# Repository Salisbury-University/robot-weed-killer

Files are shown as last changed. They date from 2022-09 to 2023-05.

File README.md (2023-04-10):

# Roundup: Robot Control App

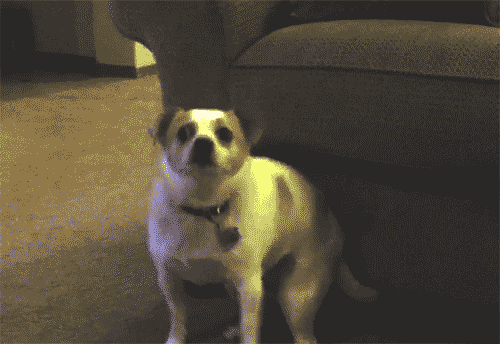
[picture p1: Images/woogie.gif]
Bouncy Dog

Dancing Dog

https://user-images.githubusercontent.com/95944392/224509408-8cf81484-2df1-4522-b72b-3398e59669f4.mp4

https://user-images.githubusercontent.com/95944392/230803867-7e4617c9-662d-4df7-9e29-15715888454c.mp4

---

## Course: COSC 426
## Client: Dr. Giulia Franchi

## Team: Kids Against Weed

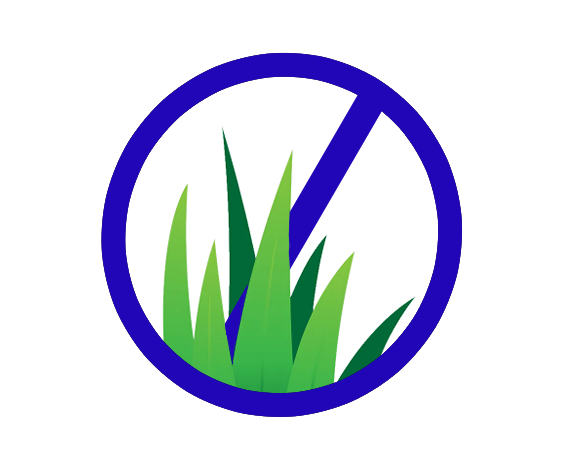
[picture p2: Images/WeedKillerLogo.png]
My Image


---
### Teammates:
* Zach Moore
* Emily Hitchcock
* Garrett Jolly
* Nick Krisulevicz
* Dane Akers
---
## Installation Instructions

```
Currently installed by running command in Flutter: will be updated with final release of product
```
---
## Contents of Repository

### Control

```
Contains Arduino code to control the robot, which includes: Laser Activation/Deactivation, and navigation
control. Both manual control and autonomous control source code resides within this directory
```

### Camera

```
Contains Arduino source code for the ESP32 camera. The ESP32 can broadcast an IP address that can be accessed
remotely from a web browser, i.e: Google Chrome, Firefox, etc. The broadcast streams video with
adjustable resolution and filters.
```

### Images

```
Contains various assets used during development of the app. App logos, splashscreens, and possibly other assets for 
styling are included.
```

### Bluetooth Controller

```
Contains the flutter app created for the project. 
```

### Object Recognition

```
Contains a python script which uses OpenCV and Numpy to detect colors. OpenCV allows for use of a filter that only 
displays certain color hues.
```
---
## Client Updates

```
Meeting 1:
-Team was instructed to finish robot design using existing hardware.
  -Suggested chassis redesign was tabled for later focus by client
  -The team is to continue with acrylic robot chassis currently in use
-Team was given the milestone of having functional autonomous program before 03/17/2023
  -The milestone requirements are as follows:
    -Have a basic autonomous driving algorithm in place
    -Have object recognition algorithm in place
    -

Meeting 2:
-Team demonstrated object recognition to client
-Team demonstrated currently functioning app to the client
-Client laid out expectations between then and the end of the first milestone. 

Meeting 3:
-Details to follow - meeting scheduled for 03/14/2023
```

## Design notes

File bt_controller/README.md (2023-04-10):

# bt_controller

Flutter project that contains the main components of the mobile application. These components are: Menu, Manual Control Screen, and Automated Screen.

## Components

### Menu

* The landing page of the applicationp; this is the first page that shows up when the app is loaded on a mobile phone.
* Allows user to select from manual control of the robot, and automated pathing
* Bluetooth menu button expands popup to select any available devices to pair
* Preferred screen orientation is portrait mode

### Manual Control

* Uses the bluetooth connection data from the menu screen to enable manual control of the robot
* Comprised of a virtual joystick and fire button, layered on top of a webview widget
* Webview used to view camera perspective when controlling the robot.

### Automated View

* Contains a map widget that is currently in a picture-in-a-picture (ideally will expand upon gesture detected and replace camera view)
* No control buttons, will only handle any issues on disconnect
* Back button to return to the menu screen -> currently testing solutions to stop the robot if the user leaves either control page

## Getting Started

If this project is inherited by another Software Engineering Group, visit the docs below to learn how to write a first Flutter app and their "cookbook" for useful samples.

A few resources to get you started if this is your first Flutter project:

- [Lab: Write your first Flutter app](https://docs.flutter.dev/get-started/codelab)
- [Cookbook: Useful Flutter samples](https://docs.flutter.dev/cookbook)
- [Navigator Class: Used to retain data across screens](https://api.flutter.dev/flutter/widgets/Navigator-class.html)

For help getting started with Flutter development, view the
[online documentation](https://docs.flutter.dev/), which offers tutorials,
samples, guidance on mobile development, and a full API reference.

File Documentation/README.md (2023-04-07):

# Roundup App Documentation
---

## Contents

* Wiring Pinouts
* Chassis Weight Distribution
* Installation Instructions

---
This folder will contain all relevant documentation of this project that is not included in the Github Wiki.

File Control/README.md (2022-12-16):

## Car Control

```
* Each folder contains the arduino code required for the vehicle to drive under the control of bluetooth or wired serial 
   connection respectively.

* The serial folder contains the Arduino code for the device to read serial input for driving and laser firing, along 
   with the Python code to drive the car through a command prompt.

    * The Python control functions are deprecated in the sense of they are not tied to the Flutter app build of the 
       project.

* The bluetooth folder contains the Arduino code for the device to read serial input over bluetooth to drive and fire 
   the laser, along with the Python code to initiate a bluetooth connection and send commands to the car. Connection to 
   the bluetooth module is needed to be initiated from device settings beforehand, or Python cannot esablish the 
   conneciton. The com port may need to be adjusted as nessecary.
```

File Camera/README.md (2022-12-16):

## ESP32 Camera

Directory contains the code to run the ESP32 camera.
```
* The camera has a web connection to stream the video to. 
* The video is accessed with the IP address. 
    * Current IP address is ##192.168.4.1
    * The app will connect to the IP address
```

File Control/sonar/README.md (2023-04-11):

#Autonomous control exists in this directory
#The current iteration of autonomous code is in (insert filename.ino here)

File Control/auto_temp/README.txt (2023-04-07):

#This directory does not hold the working autonomous files
#Find the working file in /Control/sonar

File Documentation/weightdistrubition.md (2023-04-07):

# Weight Distribution in New Chassis

## FRONT END:

```Weight of laser: 13.1 oz```

## REAR END:

* Weight of lead cylinder, 3cm diameter, 1cm height: 2.8 oz
* 2x lead cylinder = 4.7 oz
* Arduino mega weight: 1.2 oz
* Power cell weight: 10.4 oz

#### Weight distribution: 13.1 vs 10.4 = 24% more weight on rear end
#### Weight distribution is calculated based on equipment, not weight of chassis or motors & wheels

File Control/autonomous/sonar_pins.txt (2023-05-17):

1st sonar sensor: LEFT FRONT, DIGITAL, echo = 50, trigger = 52, (Original lone sensor)
Left sensor: VCC = Red wire, GND = Green wire

2nd sonar sensor: RIGHT FRONT, DIGITAL, echo = 40, trigger = 42
Right sensor: VCC = Grey wire, GND = Green wire

3rd sonar sensor: REAR, DIGITAL, trigger = 10, echo = 9
Rear sensor: VCC = White wire, GND = Grey wire

WIRING (IN ORDER OF LEFT TO RIGHT)

Left sensor: green, yellow, orange, red

Right sensor: green, blue, purple, grey

Rear sensor: grey, green, purple, white

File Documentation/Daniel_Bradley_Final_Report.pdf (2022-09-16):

SALISBURY UNIVERSITY

# Weed Removal through Laser Technology and Robotic Automation Report

Daniel Bradley
May 20, 2022

### 1. PROJECT GOALS

The primary goal of this research project is to explore an alternative method of weed control via a laser mounted robot which can target and destroy weeds through automation. During the semester I investigated how robotics, automation, and laser technology can be used as a possible method of weed control. While this is not an original idea, the use of robotics in combination with lasers as weed control is very recent. With currenting testing and studies, I believe that the combination of the three fields can be a potent form of disposing weeds, compared to herbicides.

### 2. INTRODUCTION

To control the growth and spread of weeds, accurate targeting of weeds is required. Primary methods of weed control are with herbicides and manual labor. Herbicides being the most convenient option comes at the price of having a negative impact on the surrounding environment. A study by Karl V. Miller shows that the adaptivity of weeds proves to be detrimental to the effectiveness of herbicides when it comes to repeated treatment (Miller 2004). Manual labor requires a heavy investment of time compared to herbicide yet does not harm the environment.

While less common methods are being researched, such as uprooting, an alternative to these methods is laser technology in combination with automation (Kurstjens 2001). The laser will be able precisely target weeds and disrupt their growth. A robot can transport a laser while being piloted through artificial intelligence. According to a study by C.Wöltjen,
damage to the meristem of a weed via diode laser (Figure 1) has shown to inhibit growth.(Wöltjen 2008). If a laser can be efficiently transported and navigated to a weed and fired at the meristem, then it would prove to be an effective way to counter weed growth.

## 3. Design

To achieve automation, the robot had to be able distribute its power supply to an Arduino and control multiple different components to assist in movement and guidance. To be able to move from point a to point b, four TT motors with wheels were required for movement. Two motor controllers were used (one for two motors each) so the Arduino could control the direction in which the motors would spin. The last step of automation was the ability to control the power of the laser independently. This was done by connecting a relay in between the 18650-battery pack and the AC adapter for the laser pointer. With this installed, the Arduino will have control on whether the laser will be on or not.

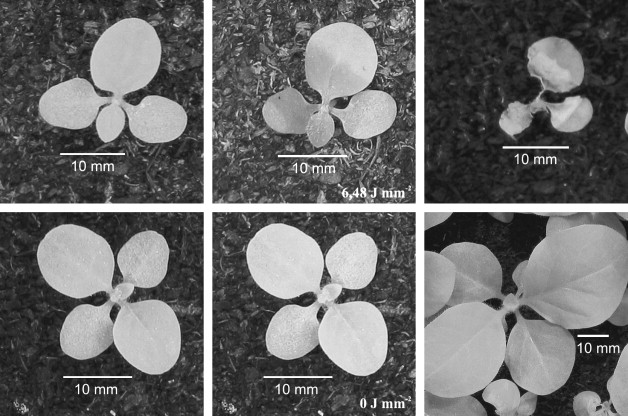
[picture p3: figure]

Figure 1. Top 3 pictures from left to right (untreated, immediately after laser treatment, week after laser treatment). Bottom 3 pictures from left to right( untreated,untreated, a week after).( Mathiassen et al., 2006)

To achieve automation, the robot had to be able distribute its power supply to an Arduino and control multiple different components to assist in movement and guidance. To be able to move from point a to point b, four TT motors with wheels were required for movement. Two motor controllers were used (one for two motors each) so the Arduino could control the direction in which the motors would spin. The last step of automation was the ability to control the power of the laser independently. This was done by connecting a relay in between the 18650-battery pack and the AC adapter for the laser pointer. With this installed, the Arduino will have control on whether the laser will be on or not.

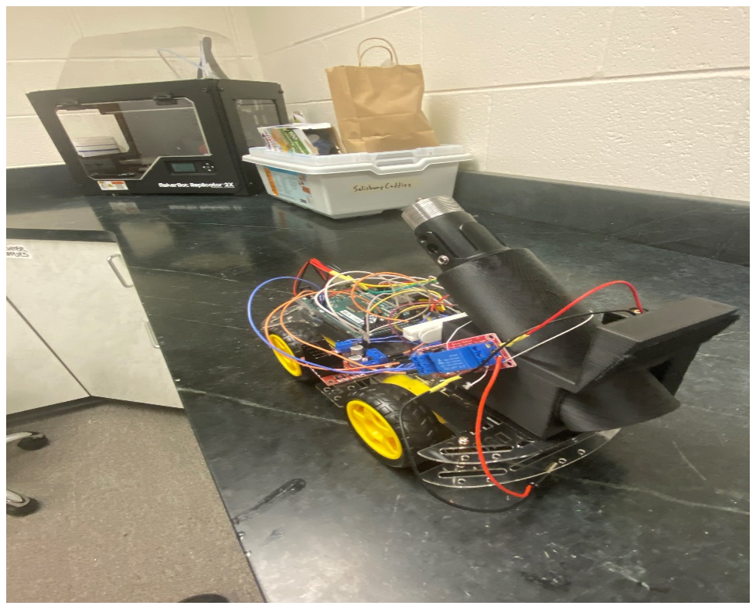
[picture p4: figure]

Figure 2:Laser – Mounted Robot

However, none of this would work without sufficient power supply. Powering the Arduino, two motor controllers, four TT motors, and the relay is done by four 9v batteries taped together in a harness. To power everything together, a breadboard was placed in the center of the robot. Here, all the positive and ground wires of the components and batteries would come together.

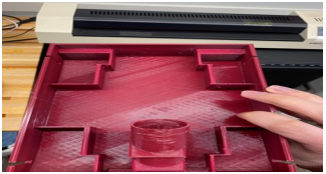
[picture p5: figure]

Figure 3:3D Printed Robot Frame

Initially the design of the robot was going to consist of a 3D printed frame designed in CAD to hold all the components of the robot. These components consist of an Arduino, 4 TT motors with wheels, 2 motor controllers, 4 9V batteries, a protoboard, and a holster to hold the laser. The prints however were not sufficient to hold the laser and other components. This was caused by either misprints by the 3D printer or inaccurate measurements in CAD. Instead, a robot frame was purchased, and a laser holster designed from CAD was 3D printed to be velcroed to the frame.

The plastic frame provided much more space than any of the previous CAD designs. The plastic frame was longer and wider than that the 3D printer workspace could provide, as well as the platform having two layers. The first layer of the plastic frame holds four 9v batteries and four TT motors. The second layer holds the laser holster, the laser, the Arduino, two motor controllers, the breadboard, and the relay. With this set up, I effectively had double the space since some components were in between to two plastic frames.

Starting from the front of the Robot, the laser holster in the centerpiece. The camera, battery pack, relay, breadboard, and laser are all in contact with the holster. While the holster is Velcroed on the frame of the robot, The camera, battery pack, and breadboard are velcroed to the holster itself. For the camera, thin strips of Velcro were attached to the frame of the camera to protect the screen and placed onto the laser holster. Since the wire connecting the battery pack and the relay is lengthy, the battery pack is velcroed to the left side of the holster while the relay is tied to the right side. The Arduino is in a plastic Arduino frame, which is velcroed to the robot frame.

A special note referring to the Velcro of the breadboard, in order to remove the Velcro the tabs on the right hand side of the white Velcro must be pulled to loosen it.

## 4. Components

Laser: A 5W 445 nm diode laser (PL-E Pro series) will be used throughout the project. The idea was that a laser that was strong enough to burn materials such as plants was required. In addition, the laser must have the ability to be controlled through a relay by an Arduino. In my research I found the laser pointer was strong enough to burn basic and organic materials as well as become automated by the Arduino.

3D Printed Laser Holster: Since both the laser and the camera must be in front of the robot, I decided that a holster that could hold both would be beneficial. The holster has a diagonal tube where the laser is placed. The diagonal angle lets the laser shoot in front of the robot and can be aimed into corners where the robot could not physically go. Facing the front of the holster is a platform where the camera is placed. The platform is angled slightly down so that the camera can see the ground in front of the robot where weeds would appear.

Husky Lens Camera: The Husky Camera has two buttons on the top side of the camera, with the screen pointing towards the user. The left side is for selecting different algorithms such as face identification, object identification, object tracking, and color identification. The right button is used to make the camera “learn” whatever is in the highlighted square on the screen. Once is recognizes an object, it will highlight the object on the screen and output information of its position on the XY axis and its size on the screen.

Laser Wiring/Power Procedure: Proper power procedure starts with making sure the cap is not on the laser, this must be twisted off for the laser to work properly. There are two ways to power the laser pointer. The first way is to insert two 18650 batteries into the battery tube and then the tube is twisted onto the laser. Then press the button on the end to the battery tube to power the laser.

The second way to power the laser pointer is through the relay. The AC adapter connected between the relay and the battery pack is inserted into the AC adapter. Insert the two 18650 batteries into the battery pack, then place the AC adapter that connects to the battery back and the laser into the AC port of the laser pointer.

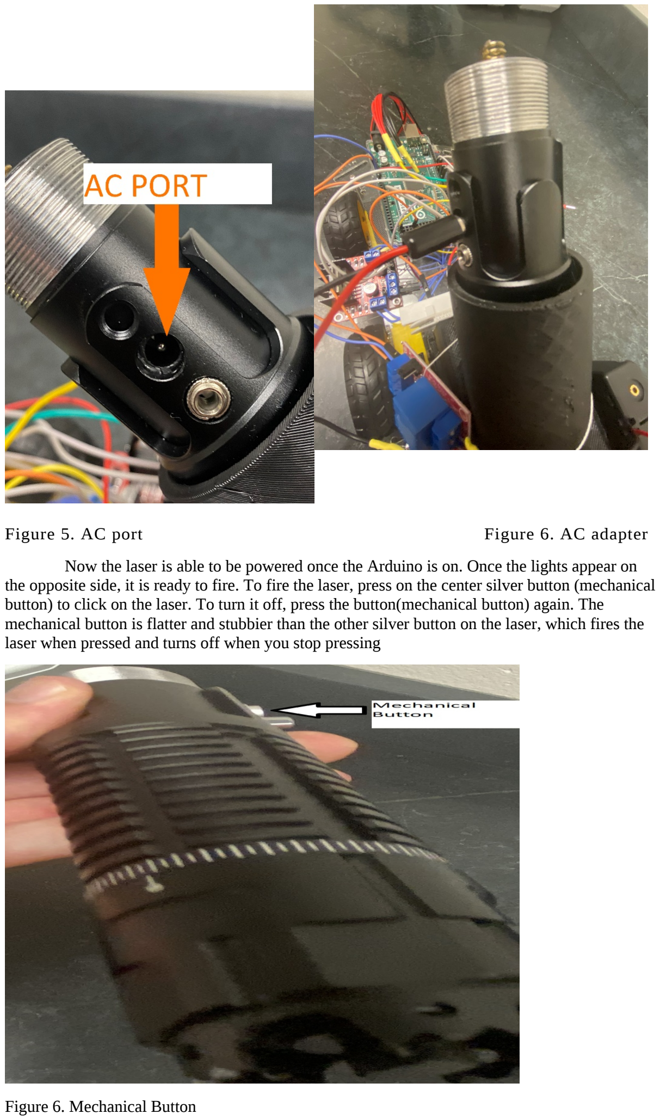
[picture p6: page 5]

Figure 5. AC port | Figure 6. AC adapter

Now the laser is able to be powered once the Arduino is on. Once the lights appear on the opposite side, it is ready to fire. To fire the laser, press on the center silver button (mechanical button) to click on the laser. To turn it off, press the button(mechanical button) again. The mechanical button is flatter and stubbier than the other silver button on the laser, which fires the laser when pressed and turns off when you stop pressing

Figure 6. Mechanical Button

Wiring the Components

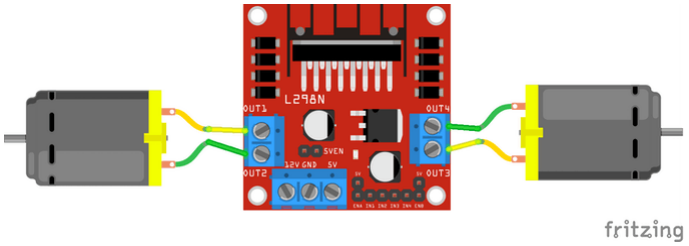
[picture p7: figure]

Figure 7. Wiring from motor controller to motors

## 4. Testing

The first test was the movement of the robot with the laser in the holster. There was initial concern that the laser would be too heavy to transport. However, testing the robot’s movement showed that there was no such issue. At times the wheels would rub against the plastic frame causing stuttering. This was fixed by adjusting the wheel in the motor axis as well as filing down the point of contact between the wheel and the platform.

Once movement was squared away, I connected the Husky Lens camera and had it identify any object that was light green. With the code I used, the robot would rotate left and right if the object was pulled to either side of the screen. Testing on making the robot go forward and backwards based on the distance of the object did not work. More testing is required to see why the robot did not act accordingly.

T h e b r e a d b o a r d i s t h e p r i m a r y s o u r c e o f p o w e r , i t p o w e r s t h e A r d u i n o M e g a , t w o m o t o r
c o n t r o l l e r s , a n d f o u r m o t o r s . A l l t h e p o s i t i v e a n d g r o u n d p o r t s o f t h e s e c o m p o n e n t s w i l l
l i k e l y b e c o n n e c t e d t o t h e b r e a d b o a r d . A s o f n o w t h e r e i s o n l y t h e g r o u n d w i r e f r o m t h e 9 v b a t t e r i e s i n t h e b r e a d b o a r d , o n c e t h e p o s i t i v e w i r e f r o m t h e 9 v b a t t e r i e s i s i n s e r t e d i n t o t h e b r e a d b o a r d t h e r o b o t w i l l b e p o w e r e d . W h i c h i s w h y t h e b e s t p r a c t i c e i s t o h a v e e i t h e r t h e r o b o t p r o p p e d o f f t h e g r o u n d w h e r e t h e w h e e l s h a n g f r e e l y , o r m a k e s u r e t h e c o d e w i l l n o t h a v e t h e r o b o t p e r f o r m a n y u n e x p e c t e d a c t i o n s . T o w i r e t h e m o t o r s t o t h e m o t o r c o n t r o l l e r s , O U T 1 ( o u t p u t 1 ) a n d O U T 2 ( o u t p u t 2 ) m u s t b e

w i r e d t o t h e i n p u t s o f t h e s a m e m o t o r . I n t h e c u r r e n t s t a t e o f t h e r o b o t , t h e o u t p u t s a r e
w i r e d t o t h e p r o p e r m o t o r i n p u t s t o a v o i d c o n f u s i o n i n t h e c o d e . O n c e t w o m o t o r s a r e
w i r e d t o t h e m o t o r c o n t r o l l e r s , t h e g r o u n d a n d t h e 1 2 v p o r t w i l l b e c o n n e c t e d t o t h e
b r e a d b o a r d . T o h a v e t h e A r d u i n o c o n t r o l t h e m o v e m e n t s o f t h e m o t o r s , c o n n e c t
I N 1 , I N 2 , I N 3 , I N 4 ( t h e i n p u t s ) i n t o f o u r s e p a r a t e d i g i t a l p o r t s o n t h e A r d u i n o M e g a . ( T i p : s e t t h e d i g i t a l n u m b e r p o r t a s a v a l u e f o r t h e d e f i n e v a r i a b l e i n c o d e ) .

As mentioned before, the motors require a HIGH,LOW output to go forward. Here in the forward function I set each motors 1,2,3,and 4 to forward. To go backwards I call the Backward function, which sets all to LOW,HIGH. This results in the robot moving backwards.

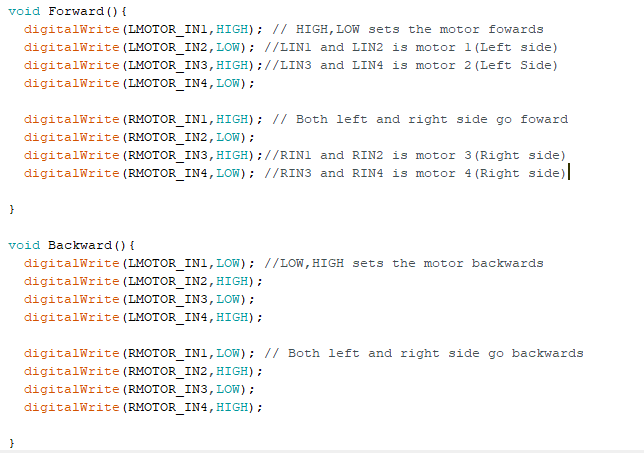
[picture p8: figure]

Figure 8. Forward() and Backward() function

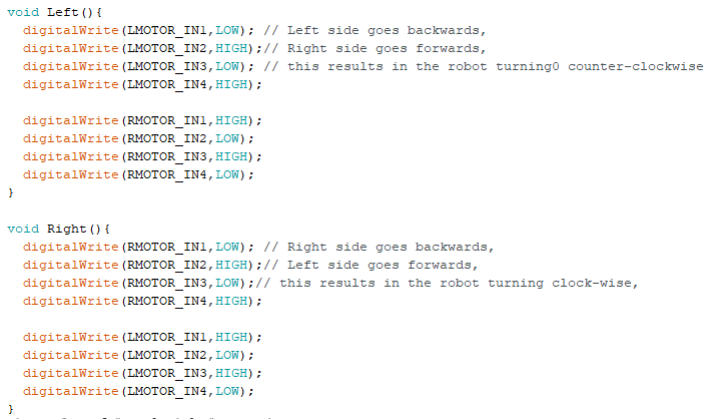
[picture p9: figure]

Figure 9. Left() and Right() Functions

To have the robot rotate, one side must spin in the opposite direction of the other side. To move left(counter -clockwise) the right motors are set to HIGH,LOW to move forward, while the left motors are set to LOW,HIGH to move backwards. The outcome is the robot will begin turning left when the Left() function is called. To have the robot rotate to the right, the motors will have the opposite directions compared to the left turn function. For turning right(clockwise), the right motors will be set to LOW,HIGH to move backwards, while the left motors will be set to HIGH,LOW to move forward. When the Right() function is called the robot will begin to spin right.

The other test had to do with the powering of the laser. Once the laser was connected to the relay. I programmed code to turn the laser on and off in 3 second intervals.

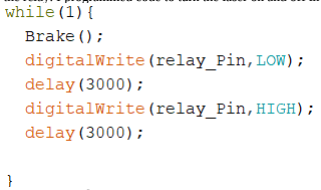
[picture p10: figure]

Figure 10. Relay Loop

In the code above, I have a while loop that last forever. In the while loop I have the Brake function called to cease movement from the robot. Afterwards, I set the relay pin to LOW with digital write then it sleeps for three seconds. The laser remains off for 3 seconds until the next digit write is called. Then the relay pin is set to HIGH and the laser is powered on for three seconds. This will repeat forever until the robot is unplugged. With the digital write function, I can set any conditional to set the relay pin to HIGH. If said condition is not meet, then the relay pin is set to LOW.

## 5. PROGRESS AND RESULTS

As of May 19
th

, the robot is able to move forwards, backwards ,turn right, turn left, and brake while carrying the laser. The robot is also capable of controlling the power to the laser. Also, components are attached to the robot to prevent any damage to the robot. Unfortunately, the Husky Lens camera module had a hardware failure during testing, so testing object tracking and laser activation through color recognition could not be done.

## 6. FUTURE WORKS

For the future, the hardware failure of the Husky Lens should be investigated. During testing of the Husky Camera module the metal components would become very hot, which I believe was the symptom of the problem. Once the camera is powered safely and efficiently, then testing of object tracking and color identification should be a priority.
When object tracking and color identification can be achieved consistently to target weeds, then testing the robot ability to follow along the sidewalk and target weeds should be done. Using the controls of the Husky Camera, the camera can learn the color of weeds using the color identification algorithm. The use of object identification on weeds can also be explored. The goal being able to accurately target weeds, minimize any misfires or overshooting, and minimize deviation from the sidewalk.
Once it can accurately target weeds, the next goal would be to explore a way to avoid obstacles. Since the Husky camera will be used to target weeds, an additional camera would have to be dedicated to obstacle avoidance. An ultrasonic senor would be able the measure the space between the robot and the ground. If an obstacle were in the way, the sensor would detect a difference distance from the distance to the ground. Then the robot could act according based on the distance measured by the sensor, like turn to the right or left and then adjust itself.

REFERENCES
Miller, Karl V.; Miller, James H. 2004. Forestry herbicide influences on biodiversity and wildlife

### habitat in southern forests. Wildlife Society Bulletin 2004, 32(4):1049-1060

D.A.G. Kurstjens, M.J. Kropff The Impact of uprooting and soil-covering on the effectiveness of

### weed harrowing Weed Research, 41 (2001), pp. 211-228

S.K. Mathiassen, T. Bak, S. Christensen, P. Kudsk The effect of laser treatment as a weed control

### method Biosystems Engineering, 95 (4) (2006), pp. 497-505

C. Wöltjen, H. Haferkamp, T. Rath, D. Herzog, Plant growth depression by selective irradiation

### of the meristem with CO2 and diode lasers, Biosystems Engineering, Volume 101, Issue 3, 2008,Pages 316-324

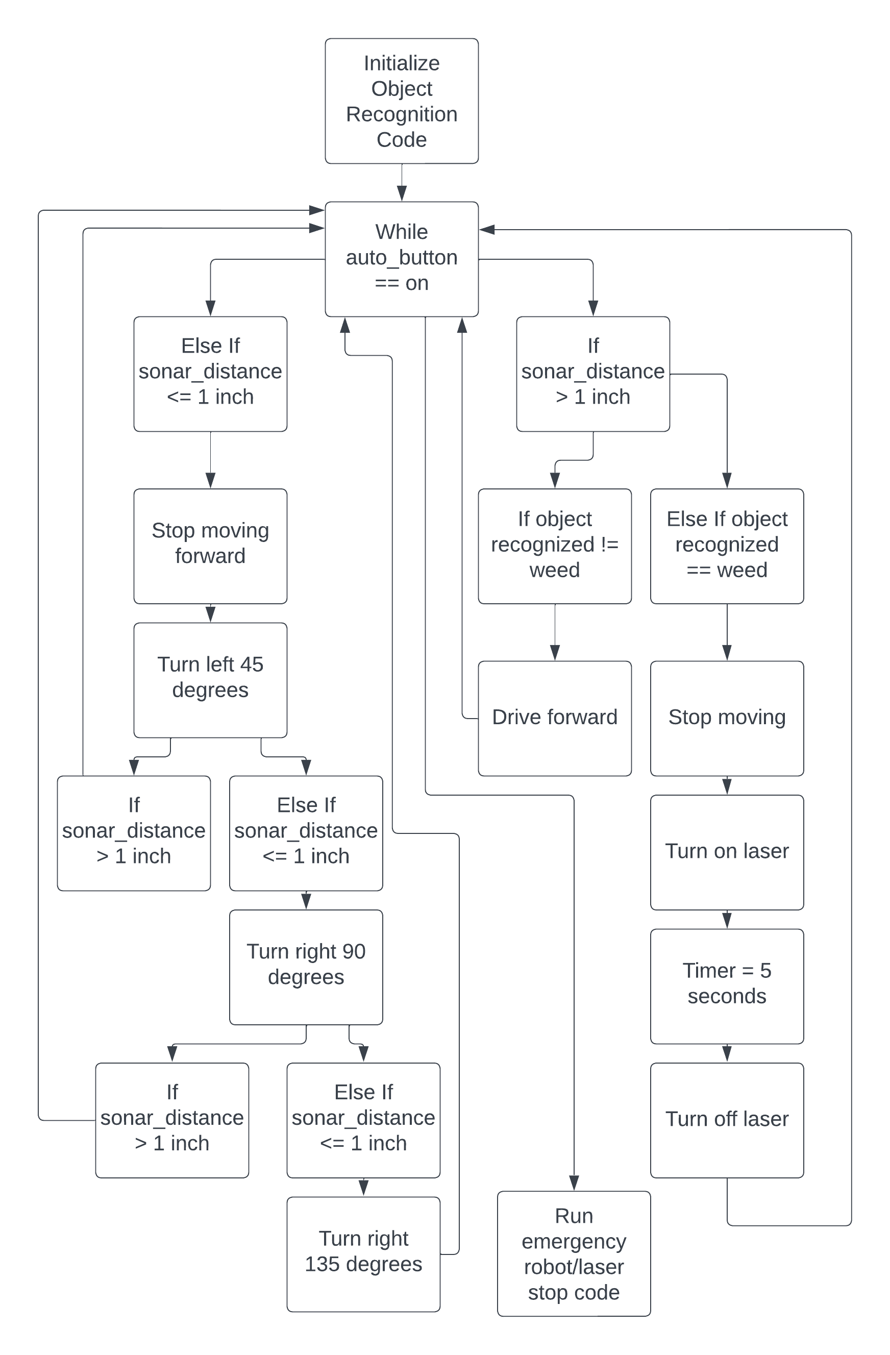
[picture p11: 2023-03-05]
Images/Autonomous Robot Concept.png

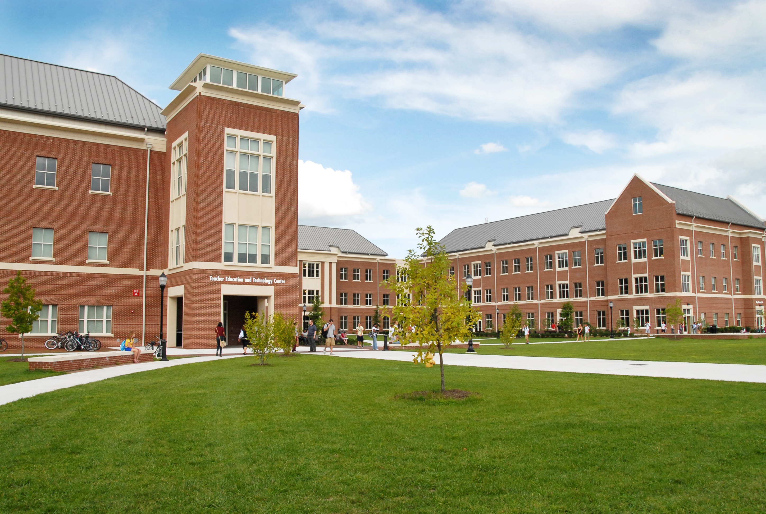
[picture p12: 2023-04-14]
bt_controller/assets/images/tetc.jpeg

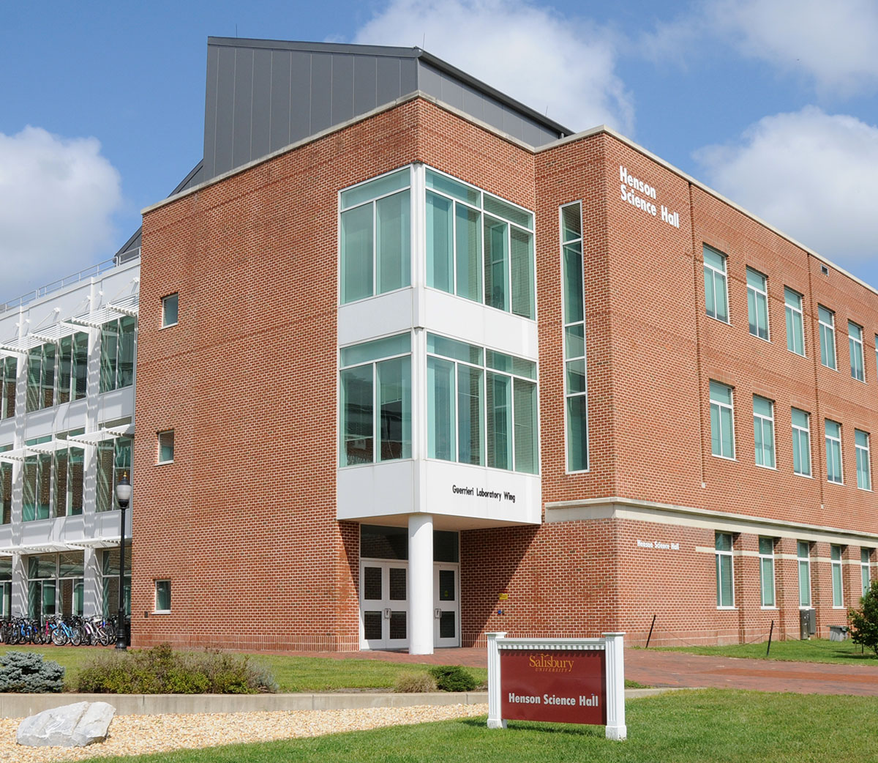
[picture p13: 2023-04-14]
bt_controller/assets/images/henson-hall.jpeg

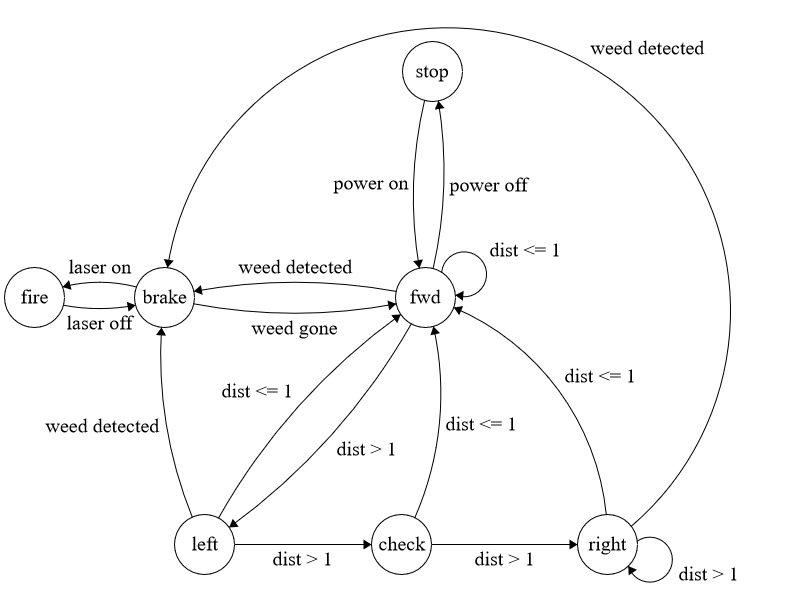
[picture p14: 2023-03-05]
Images/Finite State Machine.png

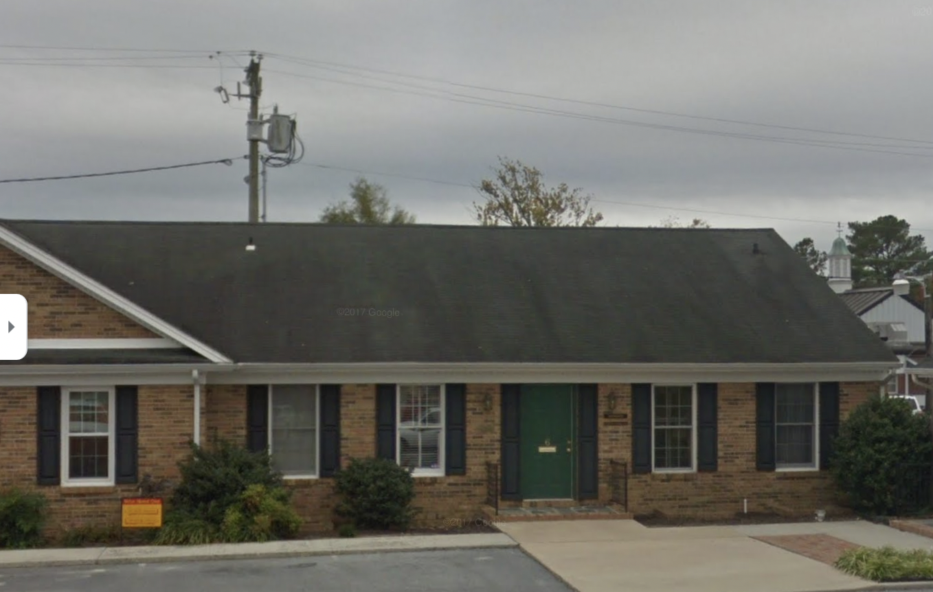
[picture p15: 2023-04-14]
bt_controller/assets/images/robotics_lab.png

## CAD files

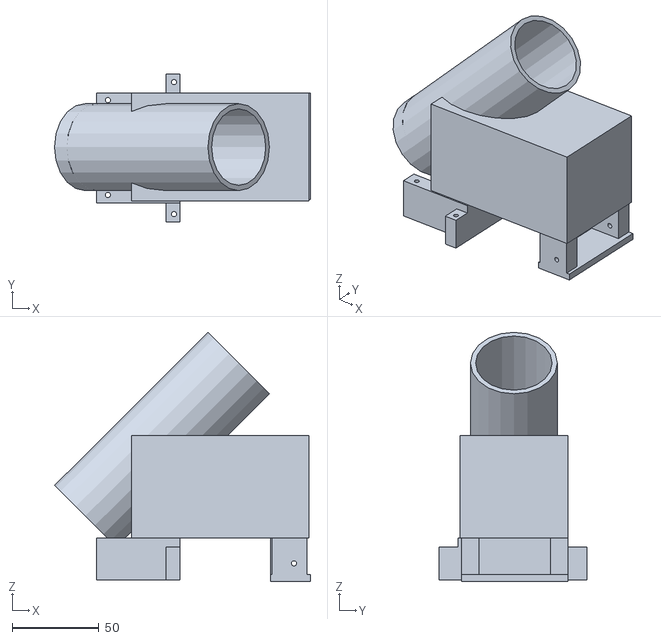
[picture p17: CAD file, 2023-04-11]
Models/Becky Chassis - Laser.stl
147.2 x 85.0 x 143.4

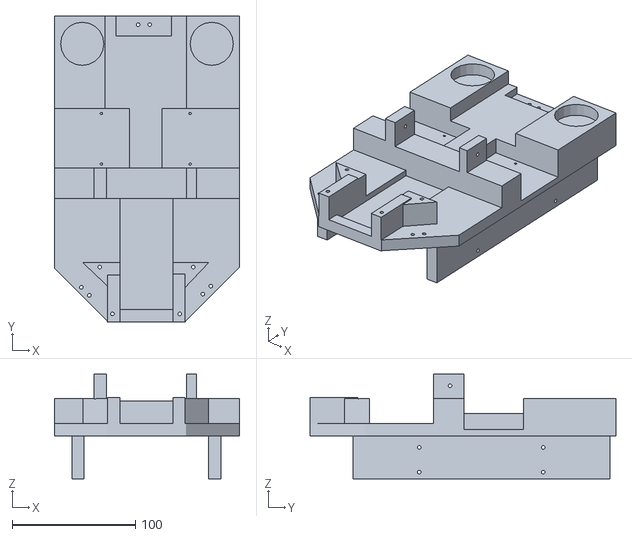
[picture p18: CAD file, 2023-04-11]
Models/Becky Chassis - Baseplate.stl
150.0 x 248.0 x 85.0

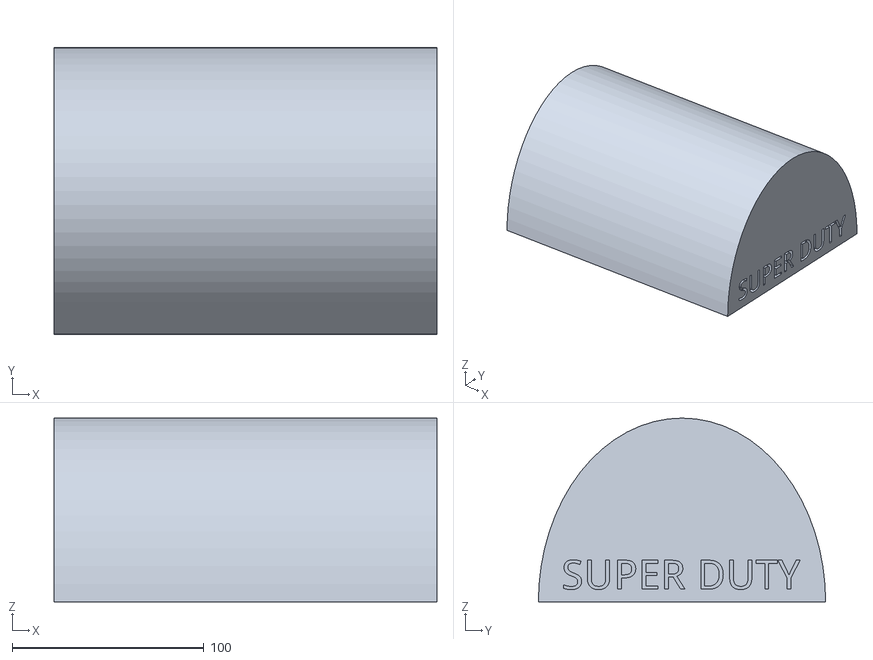
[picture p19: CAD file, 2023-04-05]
Models/Becky's Lid - First Design.stl
200.0 x 150.0 x 96.0

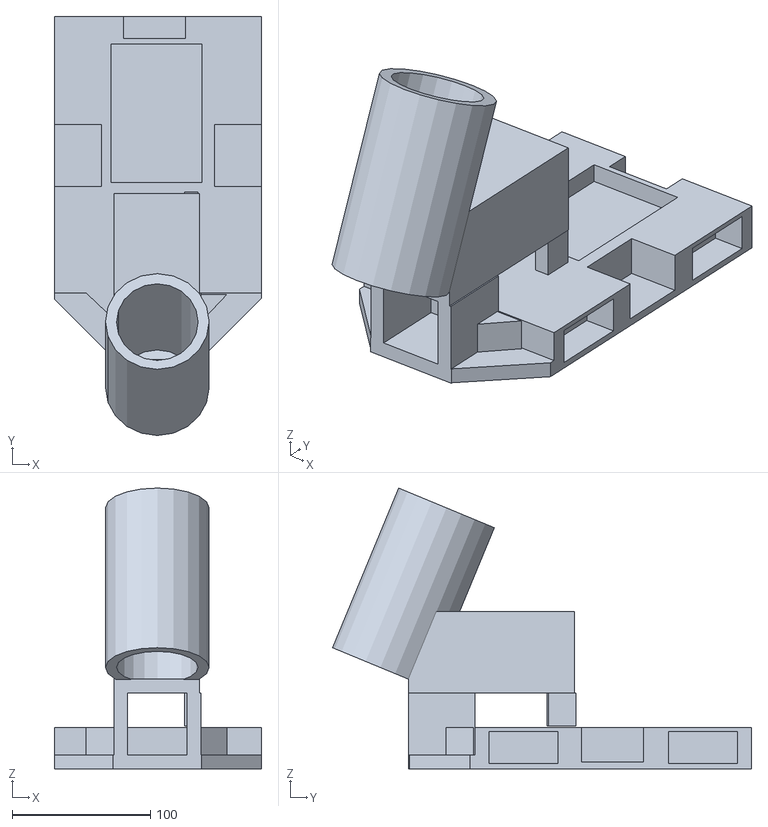
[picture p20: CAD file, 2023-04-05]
Models/Becky Chassis - First Design.stl
150.0 x 303.1 x 203.2

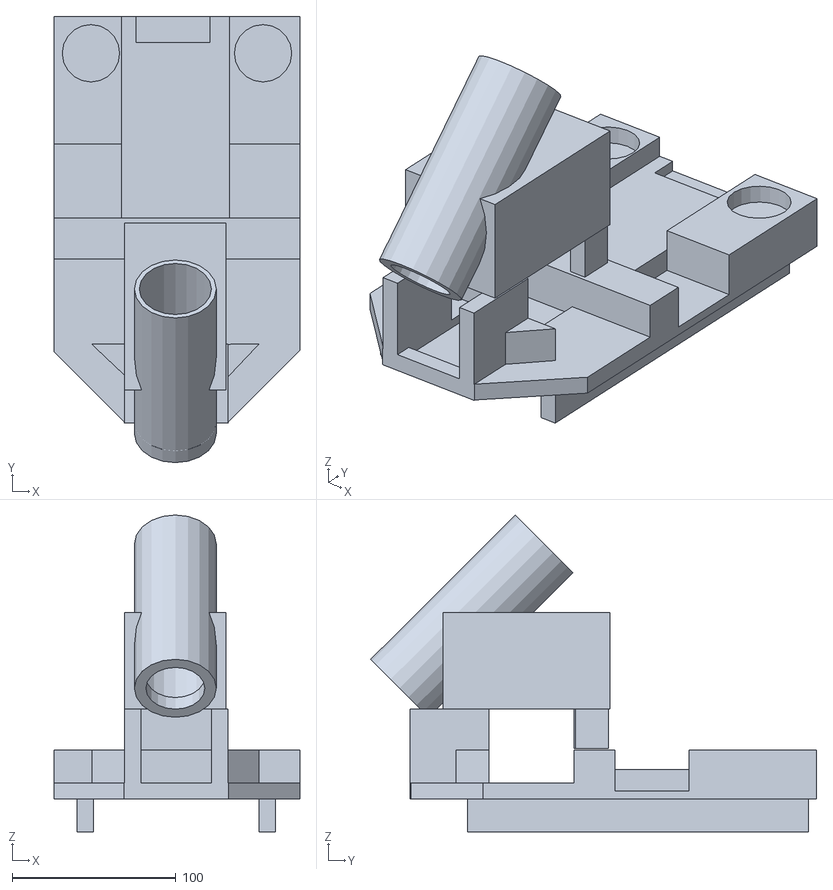
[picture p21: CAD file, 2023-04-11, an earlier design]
Models/OldModels/Becky Chassis - Second Design.stl
150.0 x 272.2 x 193.4

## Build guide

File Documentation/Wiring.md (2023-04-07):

# Wiring Pinouts
---
* Laser Relay- pin 46, pwr + gnd on arduino
* Bluetooth - state pin 5, rx pin 13, tx pin 12
* Sonar - green gnd, purple 5v, white 52, gray 50

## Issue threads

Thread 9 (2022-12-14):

Robot drives forever on disconnect

qiugai, 2022-12-14:
Tick system is too intrusive. 👎

ZM009, 2022-12-15:
Might need to switch bluetooth modules as a __last resort__.
HC-06 is only a **slave driver**, and AT mode is _not_ easily configured unlike the HC-05, HM-10, etc.

qiugai, 2022-12-15:
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

Potentially can tap into this LED header and use it to monitor the connection (depends on the age of our model).

ZM009, 2022-12-15:
> 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
>
> Potentially can tap into this LED header and use it to monitor the connection (depends on the age of our model).

Should be able to work, plastic sleeve needs to be removed to access pin 24 -- unless the STATE pin in our model is connected directly to LED. Can

ZM009, 2023-02-01:
Below code (sourced from [http://www.martyncurrey.com/hc-05-fs-040-state-pin/#:~:text=The%20STATE%20pin%20is%20LOW,value%20of%20the%20STATE%20pin.](url)), shows an example of using the HC-05 bluetooth modules state pin. This is a possible solution to detect connection/disconnection.

```
// BTconnected will = false when not connected and true when connected
boolean BTconnected = false;

// connect the STATE pin to Arduino pin D4
const byte BTpin = 4;

void setup()
{
    // set the BTpin for input
    pinMode(BTpin, INPUT);

    // start serial communication with the serial monitor on the host computer
    Serial.begin(9600);
    Serial.println("Arduino is ready");
    Serial.println("Connect the HC-05 to an Android device to continue");

    // wait until the HC-05 has made a connection
    while (!BTconnected)
    {
      if ( digitalRead(BTpin)==HIGH)  { BTconnected = true;};
    }

    Serial.println("HC-05 is now connected");
    Serial.println("");

    // Start serial communication with the bluetooth module
    // HC-05 default serial speed for communication mode is 9600 but can be different
    BTserial.begin(9600);
}
```

ZM009, 2023-02-08:
Robot stops immediately on disconnect due to added code and hc-05 module switch

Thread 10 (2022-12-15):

spaghetti on dog head

qiugai, 2022-12-15:
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

ZM009, 2022-12-15:
They can see these issues lol

qiugai, 2022-12-15:
good

ZM009, 2022-12-15:
Just take the spaghetti off the dawg's head

qiugai, 2022-12-15:
smart, this is why we pay you the big bucks

Closed 2022-12-15.

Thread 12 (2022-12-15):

Joystick Animation Glitching

ZM009, 2022-12-15:
## Expected Behavior

Joystick should run smoothly at ~30-40 frames per second when connected via bluetooth, while sending bt messages to the Arduino.

## Actual Behavior

When connected to bluetooth and sending navigation messages, the joystick animation stutters and glitches back and forth.

## Steps to Reproduce Behavior

* Launch app on smartphone
* Connect to the Arduino via the bluetooth menu
* Move joystick around while connected

### Possible Solution
##### Adding a Duration object to the Joystick View(?)
```
interval: Duration* ()
```

ZM009, 2023-02-15:
Will possibly fix at a later date; No solution at the moment.

qiugai, 2023-03-11:
Will not be fixed. More than likely phasing out joystick and focusing more on automated control first. (Slim chance to reopen later)

Closed 2023-02-15.

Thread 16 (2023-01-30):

Day One Meeting Updates

nickkrisulevicz, 2023-01-30:
Decided on new design for robot vehicle. Details:
- body on frame design
- more ground clearance
- better battery
- better motors
- mechano wheels
- 3D printed frame with laser mount as the same piece as frame
- 3D printed body: one piece that will slide on top of body to allow easy removal for maintenance and battery charging
- new bluetooth module: HM-10

Application software changes:
- UI: joystick tuning, enlarge the webview
- allow switching between manual control and automatic control
- Backend: separate device to perform imaging

Ultimate goal for semester:
-finish improved hardware
-finish autonomous driving for robot
-polish app

Closed 2023-02-27.

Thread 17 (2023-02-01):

Resize Webview to fit screen

ZM009, 2023-02-01:
### Current Feature

The webview is contained in the middle of the screen at a fixed size, when it is set to on and set to off.

### Updated Feature

Ideally, the container of the webview will be expanded to the entire screen to allow the webview to dynamically fit any android screen regardless of dimensions.

evHitch, 2023-02-15:
Webviewx now fills the screen. Additional widgets have yet to be positioned.

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

Closed 2023-02-15.

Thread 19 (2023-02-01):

Pixel Overflow on Screen Expansion

ZM009, 2023-02-01:
## Expected Behavior

When the webview is expanded to the entire screen of a phone, the buttons to control the robot manually should stay on top of the view, allowing the user to see the robot's camera view while still controlling its movement.

## Actual Behavior

When the screen is resized beyond certain dimensions (w x h), the joystick and other relevant buttons are pushed off the screen which causes a pixel overflow, and a while portion of the screen.

------
#### Possible Solution

Row containing buttons may need to be expanded or redone from the ground up.

ZM009, 2023-02-08:
@evHitch i'll checkout webviewx

evHitch, 2023-02-15:
Implemented WebviewX & resolved the overflow issue. I'll be fixing the layout of the page next.

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

ZM009, 2023-02-15:
Design needs work as it is rudimentary, otherwise approved.

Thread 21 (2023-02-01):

Redesign of Frame - Equipment Research

nickkrisulevicz, 2023-02-01:
Must research and decide on which new parts to include. This is necessary for two reasons. First, the parts must be known so their dimensions can be incorporated into the new designed frame. The new frame is being 3D printed and slots for each piece of equipment on the frame will be added in the 3D modeling phase. We cannot design the new frame nor print it until we choose the new parts. This is the first priority for the hardware design part of the project as it holds up progress on building the robot.

nickkrisulevicz, 2023-02-07:
After consulting with client, redesign of frame and body of robot will not take place within first milestone - before spring break. This issue will not be removed, but will not be addressed at this time

ZM009, 2023-02-09:
As of right now, can not be redesigned. Maybe will be updated after spring break and further feature developments.

Closed 2023-02-09.

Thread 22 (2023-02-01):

Alternative Power Source

ZM009, 2023-02-01:
### Current Hardware

The robot is chassis is powered by four 9V batteries, which provide inefficient amperage and are prone to dying rapidly after prolonged use of the robot's motors.

### Future Goal

Find a rechargeable battery to power the motors and BT module with sufficient amperage and voltage output.

ZM009, 2023-02-08:
Amperage should be strong enough too so it isn't useless below 6V of charge. LGTM

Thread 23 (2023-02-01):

Sonar Part Research

ZM009, 2023-02-01:
### Goal

Research the sonar attachments and other methods of obstacle avoidance to allow autonomous robot control.

#### Future Addition

Possible implementation of sonar as a method of obstacle avoidance on the weed robot utilized in public spaces and other areas with walls, curbs and other obstacles.

ZM009, 2023-02-09:
#### An algorithm can be designed to have the robot check the left and right paths to determine which way to travel when an ultrasonic sensor detects an obstacle.

```
_Obstacle to the front and on the left:_
* The robot will turn and go right

_Obstacle to the front and on the right:_
* The robot will turn and go left

_Obstacles surrounding robot:_
* The robot will reverse and change path to avoid obstacles
```

ZM009, 2023-02-09:
Research phase completed; Proceeding to algorithm design and test implementations

Closed 2023-02-09.

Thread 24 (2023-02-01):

Plan setup of server to receive / process ESP32 footage

qiugai, 2023-02-01:
In order to receive the live camera feed for image processing to allow the robot to move autonomously, there must be a server to perform this processing.

We must add a new node into the map in order to process image data, along with sending communications to the Android phone to instruct the robot where to move, and read whether to activate or pause autonomous navigation.

qiugai, 2023-02-02:
mockup :)

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

ZM009, 2023-02-15:
Planning phase completed; rough idea of what's desired so far

Closed 2023-02-15.

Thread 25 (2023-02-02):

OpenCV color filter live ESP32 camera feed

qiugai, 2023-02-02:
camera feed will be transmitted to the server over wifi to be processed by the python script

qiugai, 2023-02-06:
https://www.cvlib.net/

provides simple, high level object detection

possible to train on weeds

qiugai, 2023-02-06:
https://stackoverflow.com/questions/60029614/esp32-cam-stream-in-opencv-python

for opening ESP32 livestream

Closed 2023-02-09.

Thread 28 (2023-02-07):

Goals Before Spring Break

nickkrisulevicz, 2023-02-07:
After consulting with client (Dr. Franchi), our team had a milestone laid out to be reached by spring break:

Priority one: The app needs to be functional and able to toggle between manual and autonomous operation. The app must be able to control the robot in its current state before major hardware upgrades are made. Initial autonomous operation must be achieved in an environment with no obstacles and square boundary. Additional pathfinding and navigation will be implemented later. For now, we need to focus on getting the robot to drive autonomously in a basic setting first.

Next milestone will follow after spring break once current one is done.

nickkrisulevicz, 2023-02-08:
UPDATE: This milestone was created in milestones, and it should not have been made in issues, this issue can be closed out

ZM009, 2023-02-08:
No longer needed

Closed 2023-02-08.

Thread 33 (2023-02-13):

DC Motors - Finding Proper Resistance

nickkrisulevicz, 2023-02-13:
##  Expected Results

The robot should use the input voltage of the 12V rechargeable battery to evenly distribute its voltage and current among each TT motor with a breadboard.

## Current Test Results

The robot currently moves too fast, and the 12V battery is currently sending too much current (amps) to the DC motors. This could result in them completely burning out.

### Solution

Documentation has been found to find the resistance needed given the voltage and amperage:

To find voltage:
*  $V=I*R$ (V: Voltage, I: Current (measured in mA or A), and R: resistance (measured in ohms $\Omega$)

To find resistance given input voltage and current:
* $R = \frac{V}{I}$

#### Current priority: Find the suggested current of the DC motors

[Current measurements of TT motors](https://nam10.safelinks.protection.outlook.com/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)

ZM009, 2023-02-15:
Voltage was found to be a recommended 7.2 V per motor.
Recommended current is 160mA (0.168 A)

Resistance found: $R=\frac{7.2}{0.168}$
$R=42.85\Omega\approx 43 \Omega$

ZM009, 2023-02-15:
Robot wouldn't drive with issues, will be revisited later.

Closed 2023-02-15.

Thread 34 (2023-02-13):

Inconsistent Access Point

ZM009, 2023-02-13:
## Expected Behavior

The ESP32 Camera should consistently broadcast the wifi network to different devices when nothing is connected.

## Actual Behavior

The Access Point of the camera is very inconsistent when broadcasting the wifi, and sometimes disconnects while displaying video feed, shutting off any view of what the robot sees.

### Potential Solution

* Possibly add more power
* Give camera a dedicated circuit

nickkrisulevicz, 2023-02-13:
A dedicated circuit was given to the camera, causing it to no longer draw insufficient power from the main circuit, this caused the camera to function completely and the access point now works consistently

ZM009, 2023-02-13:
### Testing

#### Multiple tests were completed by Dane and Nick with the video feed. Supervised by Zach and Garrett. Solution Approved. 👍

Closed 2023-02-13.

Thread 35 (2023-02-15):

Design Autonomous Operation Arduino Code - Early Stages

nickkrisulevicz, 2023-02-15:
The algorithm for the autonomous driving capability of the robot is a priority. This code must be included in the final app. A functional prototype must be done by the first milestone goal before spring break.

The first resulting deliverable for this step will be a pseudocode algorithm or a flowchart diagram. A solution as to how the robot is going to operate on its own will need to be devised.

More to follow in the immediate future.

nickkrisulevicz, 2023-03-05:
Past early stages in development, onto the code now that Finite State Machine has been created

Closed 2023-03-06.

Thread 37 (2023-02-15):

💡 - Bluetooth Button and Code Refactor

ZM009, 2023-02-15:
### Start Date

_No response_

### Implementation PR

_No response_

### Reference Issues

References Issues #7 and #18

### Summary

#### Goal: Move bluetooth button to Menu Screen

The bluetooth button will be removed from the webviewx screen in manual control, and added to the menu screen instead. This will require refactoring some of the bluetooth code functionality in order to allow manual control to still send commands to the HC-05 module.

### Basic Example

#### At menu screen:

* Possible vertical screen orientation
* Bluetooth icon to allow user to connect to any BT module for robots
* Connection should persist over to the manual or automated views

### Drawbacks

#### Possible Drawbacks:

* Connection might not be persistent
* Refactoring of bluetooth functionality may need to occur
* Possible import from menu screen to ensure bluetooth widget works on separate pages

ZM009, 2023-03-13:
Discussed bluetooth functionality relocation with Emily, reviewed bluetooth code to her her move the button and all of its functionality to the menu screen.  Currently finished with the relocation and slight code refactor.

Closed 2023-03-13.

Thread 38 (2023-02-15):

🛠 - Ultrasonic Sensor Installation and Testing

ZM009, 2023-02-15:
### Start Date

_No response_

### Reference Issues

Issue #23

### Summary

#### This refers to the hardware installation and placement on the weed robot.

#### Things to be considered:

* Pin placement on arduino
* Positioning of sensor
* Possible reorganization of wires and mounts
* Possible sonar mount creationi

### Basic Uses

#### Post-installation:

Sonar can be tested in small cases by running the DC motors continuously and blocking the sensor with a person's hand to test for responsiveness and find any possible window of error.

ZM009, 2023-03-08:
Sonar has been tested, and reviewed by Garrett and I. Works for distance calculation and brake response.

Closed 2023-03-08.

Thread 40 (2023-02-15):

💡 Create and Implement Basic Object Avoidance Algorithm

ZM009, 2023-02-15:
### Start Date

_No response_

### Implementation PR

_No response_

### Reference Issues

#38 #23

### Summary

#### Brief Algorithm Details:

* Stops motors when a few inches from an object
* Check around the object for other obstacles
* If obstacles are in all directions the robot will reverse and turn around to avoid all obstacles and return to path[^1]

[^1]: Based off basic object avoidance algorithms; will be wrapped in a conditional

### Basic Example

Written in c++/Arduino sketch, this feature will be used to avoid any and all obstacles detected by the ultrasonic sensor in a basic predetermined path.

### Drawbacks

#### Possible Impact:

* Only basic pathing
* Sonar may potentially fail
* Allows for further experimentation on sonar and possible coverage of multiple angles while driving

nickkrisulevicz, 2023-03-05:
Finite State Machine has been created from the simple flowchart algorithm. Now, the code needs to be created. Will be implemented in: main/Control/autonomous/auto.ino

ZM009, 2023-03-13:
Basic algorithm implemented -- in another issue, the algorithm will be heavily refined and possibly included with a mapping/path planning algorithm.

Closed 2023-03-13.

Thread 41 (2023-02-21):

Improvements and Reorganization of GitHub Wiki - Documentation (Ongoing)

ZM009, 2023-02-21:
#### Started: 2/21/2023

## Goal
----
* Must add detailed instructions under each header to describe project overview, installation instructions, etc. within the main wiki page
* Start to record better documentation of Flutter extensions, dependencies, and Arduino modules.
* Consolidate documentation in one area for any and all libraries used.
* Record and store all sprint updates in separate section.
* Create biweekly client update sections

nickkrisulevicz, 2023-04-16:
Will need to wait until all branches are merged before writing all READMEs or else chaos keeping track of all documentation could ensue.

nickkrisulevicz, 2023-04-16:
The Wiki is more important to anyone who views the repository than individual READMEs in each directory

Closed 2023-05-17.

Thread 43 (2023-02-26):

💡 [REQUEST] - Basic Object Recognition

qiugai, 2023-02-26:
### Start Date

2/26/2023

### Implementation PR

_No response_

### Reference Issues

_No response_

### Summary

The Python server program needs to be able to recognize a weed from other objects up close.

Using something like YOLO (You Only Look Once) or similar, implement this into the current detection program we run on the RUPER server.

### Basic Example

ESP32 stream shows up on RUPERT, the server sees an object through the camera stream, and is trained to recognize a weed. Upon recognition, this starts the exterminate protocol, pausing the patrol algorithm and centering the laser on the weed before firing.

### Drawbacks

Time consumption, this will take a bit to get juts right.

Factoring in the hardware we're using (camera blind spots, aligning for laser firing on weed , etc.)

Closed 2023-02-27.

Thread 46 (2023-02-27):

💡 Take Sonar Module Input with Arduino

nickkrisulevicz, 2023-02-27:
### Start Date

02/27/2023

### Implementation PR

_No response_

### Reference Issues

#38 #35

### Summary

Need to write Arduino code to take the input from the HC-SR04 module. The purpose of this is to make sure that the autonomous control has input from the sonar equipment so that it can be used to make the robot stop when there is an object in its path during autonomous function.

### Basic Example

Feature will consist of Arduino code.

### Drawbacks

Need to troubleshoot any potential bugs in the Arduino code during implementation.

qiugai, 2023-03-11:
Observed new sonar library implementation and test case results.

Closed 2023-03-11.

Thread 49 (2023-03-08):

💡 Setup MapBox API Credentials

ZM009, 2023-03-08:
### Start Date

03/07/2023

### Implementation PR

_No Pull Requests Used as of now_

### Reference Issues

_No Issues Referenced_

### Summary

MapBox is an API used by OpenStreetMap. This is a general setup of any access tokens needed for eventual autonomous pathing using various algorithms like Dijkstra 's Shortest Path, etc. For now, basic setup is the primary goal which will include generating an authenticating key, secret keys for map manipulation, etc.

### Basic Example

With the setup of the API, this would allow for an interactive map to be created, eventually leading to a user able to choose a start and stop point for the laser robot, and implement any pathing algorithms used/designed for max efficiency.

### Drawbacks

Possible Drawbacks Include:
* If request limit is surpassed, it will cost monthly per an additional amount of requests per month. (Very minimal chance)
* Current Robot Design:
     * May need a sort of GPS module installed; which has a moderate range of error.

qiugai, 2023-03-11:
API Credentials have been added to the gradle files. Meeting with client to determine when to implement mapping

Closed 2023-03-11.

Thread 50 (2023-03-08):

🐛  Sonar Module Defect

ZM009, 2023-03-08:
### Description

Sonar Module pinout was defective, and printing out 0 cm and 1149 cm, which effectively will prevent the car from braking properly in autonomous mode.

### Reproduction steps

```bash
1. Upload the Arduino Sketch
2. Open Serial Monitor from the 'tools' tab
3. Place Sonar Module near Obstacles
4. Read misprinted values in Serial Monitor
```

### Screenshots

```bash
N/A
```

### Logs

```bash
Uploading new sketch to Arduino Mega 2560 on /dev/cu.usbmodem1401 ...

Distance = 0cm
Distance = 0cm
Distance = 0cm
Distance = 1149cm
Distance = 1149cm
Distance = 0cm
Distance = 0cm
Distance = 0cm
```

dakers01, 2023-03-08:
Replaced module, and re soldered pins in a new position.

Logs:
```
Distance = 4cm
Distance = 10cm
Distance = 64cm
Distance = 195cm
Distance = 3cm
Distance = 54cm
```

dakers01, 2023-03-08:
Review @ZM009

Closed 2023-03-08.

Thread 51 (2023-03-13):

💡 Develop Autonomous Algorithm to Navigate Corners

nickkrisulevicz, 2023-03-13:
### Start Date

03/13/2023

### Implementation PR

_No response_

### Reference Issues

#40 #35

### Summary

Basic implementation of the autonomous algorithm has been achieved. This was taken care of in issue #40. The current state of the algorithm results in undesirable behavior with the robot navigating when it is positioned in a corner. The objective of the resolution of this issue is to continue to develop the autonomous code to ensure that the robot can navigate out of corners.

### Basic Example

The resulting code from this feature will consist of Arduino code. The location of the files are /Control/sonar. The files are currently in branch: sonar_patrol. This will not be merged with main branch for the time being.

### Drawbacks

Potential drawbacks to this feature are time requirements and capabilities of the hardware. The motors can only be set to either HIGH or LOW, without precise modulation of speed. This can result in inconsistent turning duration, forward and reverse distance, as well as other complications while driving. The solution can be to carefully observe and test various values within the driving program.

ZM009, 2023-04-07:
Sonar Patrol was modified, forgot to close.

Closed 2023-04-07.

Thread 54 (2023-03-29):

🛠 Create Initial Chassis Redesign Mockups

ZM009, 2023-03-29:
### Start Date

03/29/2023

### Reference Issues

_No response_

### Summary

After visiting the makerlab, there were two concrete solutions given. The chassis piece could be spray painted to an opaque color and scanned, but the measurements of the scan may not line up, rendering the time spent useless. The other, more viable option is to do a near complete redesign of the chassis and print it with a different type of material.

### Basic Uses

These designs will be used to pick out a chassis shape and design of the holes/slots for a greater durability. This is to prevent more cracks and allow for the robot to be tested with sonar without the fear of the piece breaking.

ZM009, 2023-04-04:
Initial Mockups were created; Design finalized.

Closed 2023-04-04.

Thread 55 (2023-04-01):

🐛 Can't view camera stream on current server program

qiugai, 2023-04-01:
### Description

When trying to access the livestream at the ESP32 IP address, the yolov5 and OpenCV programs both time out, thus cannot run the weed detection model on them.

### Reproduction steps

```bash
1. Connect to ESP32 hotspot
2. Launch yolov5 or OpenCV with source of 'http://192.168.4.1'
```

### Screenshots

_No response_

### Logs

_No response_

ZM009, 2023-04-03:
😭 😞 😢

ZM009, 2023-04-03:
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

Closed 2023-04-03.

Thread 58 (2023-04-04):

🛠 Modify and Print Final Chassis Design

ZM009, 2023-04-04:
### Start Date

04/05/2023

### Reference Issues

#54 #51

### Summary

The final design for the chassis will be printed and modified upon printing to add all necessary parts to the robot for further improvement of the autonomous algorithm.

### Basic Uses

## Improvements Explained
* Camera placement changed to prevent shake
* Move motor mounts for more freedom of design
* Used to further develop autonomous algorithm
* Integrated laser mount to prevent shake upon braking

nickkrisulevicz, 2023-04-05:
Designed new chassis iteration. Calculated weight distribution included in new directory located in sonar_patrol branch.

ZM009, 2023-04-07:
Chassis pieces printed in MakerLab

Closed 2023-04-07.

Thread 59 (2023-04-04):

💡 Create and Implement Getters for Latitude and Longitude

ZM009, 2023-04-04:
### Start Date

04/05/2023

### Implementation PR

_No response_

### Reference Issues

#57

### Summary

Private getter functions would be created to utilize the latlng package's features in order to grab latitude and longitude measurements of custom points when the user holds an area of the map down.

### Basic Example

* Can create possible start and end points for robot path planning
* Could be used to track gps coordinates

### Drawbacks

Coordinates could have a bigger window of error; could require further refinement of the getters.

ZM009, 2023-04-10:
can use flutter_map's functionality to grab the latitude and longitude of a gps. Very high level implementation depending on the purpose.

nickkrisulevicz, 2023-04-16:
flutter_map works with the current GPS module just fine?

ZM009, 2023-04-16:
Yes. There's two libraries in flutter we can use to handle this: nmea, and latlong2. Latlong2 contains predefined types to contain the coordinates, while the nmea library is a parser that can be used to extract the given robot coordinates from the gps information sent by the arduino. These two can be tied in with flutter_map to reload the map's tiles and continually track the robot's location

ZM009, 2023-04-16:
After implementation there's a possibility of giving a robot a start and end point for path planning, but that may not be implemented due to time constraints.

ZM009, 2023-05-17:
No time left to learn nmea parsing

Closed 2023-05-17.

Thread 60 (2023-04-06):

💡 Merge object tracking to main server program

qiugai, 2023-04-06:
### Start Date

4/5/2023

### Implementation PR

none :)

### Reference Issues

#60

### Summary

The current server program uses color filtering to identify green masks, this is ugly.

Merge the boxed tracking to the server program to have a prettier result to see the image processing.

This includes printing out coordinates of identified objects so they can be used as direction for the autonomous driving code.

### Basic Example

Move code from one file to another

### Drawbacks

Nothing except my sanity--;

Closed 2023-04-10.

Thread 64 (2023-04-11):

🛠 GPS Module Addition

ZM009, 2023-04-11:
### Start Date

04/11/2023

### Reference Issues

#59

### Summary

With the installation of a gps module, different flutter libraries can be used to establish a UART connection to the Arduino and parse through gps information sent to the app. This would allow for the creation of latitude and longitude getters.

### Basic Uses

* Can be used to track the robot as it moves autonomously.
* Possible implementation of telling robot to drive from point a to point b

ZM009, 2023-04-14:
oversaw gps installation.

Closed 2023-04-14.

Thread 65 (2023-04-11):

💡 Create Test File for GPS module

ZM009, 2023-04-11:
### Start Date

04/11/2023

### Implementation PR

None 😉 👨🏻

### Reference Issues

#64

### Summary

A file will be created to test the functionality of the NEO-6M module and will print out the coordinates, and time printed.

### Basic Example

Will be used to grab coordinates, and the time the coordinates were received.

### Drawbacks

There could be a margin of error involving the gps and precise coordinates.

ZM009, 2023-04-14:
created a file to display coordinates information

ZM009, 2023-04-14:
coordinates printed when robot moved in different areas

Closed 2023-04-14.

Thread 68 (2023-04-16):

💡 Finish Autonomous Operation - Hardware is Complete

nickkrisulevicz, 2023-04-16:
### Start Date

04/15/2023

### Implementation PR

_No response_

### Reference Issues

#38 #21 #23 #35

### Summary

Now that hardware fixes and additions are complete, the next objective is to finish the autonomous driving algorithm for obstacle avoidance. More on object recognition and driving to follow.

### Basic Example

Deliverable product from this issue will be Arduino code in a .ino file

### Drawbacks

Will need to add object recognition and auto driving cooperation following resolution of this issue.

ZM009, 2023-05-07:
Nice. 👨

Closed 2023-05-07.

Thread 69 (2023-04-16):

💡 Develop Solution for Object Recognition and Arduino Robot Control

nickkrisulevicz, 2023-04-16:
### Start Date

04/15/2023

### Implementation PR

_No response_

### Reference Issues

#48 #40 #46 #45 #32 #35 #23 #24 #38 #50 #51

### Summary

The final step before finishing the app is to come up with a solution to mate the weed detection algorithm and the robot autonomous driving algorithm. Arduino

### Basic Example

Ideal solution is to have auto.ino and object detection on ESP32 running at all times. If ESP32 detects a weed, it sends a signal to the auto process. auto.ino then calls a laser function that rotates the robot until the weed is centered in the camera, then drives forward until the weed is centered under the laser's point of impact. Robot stops moving, then laser turns on for a certain amount of seconds. After laser turns off, the main loop of auto.ino continues until object recognition detects another weed

### Drawbacks

Will need to learn how to take output from object recognition code and use that as input for auto.ino. This will be a tricky solution to achieve since Arduino can only have Arduino code loaded into its memory, and the weed detection program is not written in Arduino code

Closed 2023-05-17.

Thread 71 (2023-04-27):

💡 Arduino Code Manual / Auto Toggle

qiugai, 2023-04-27:
### Start Date

4/27/23

### Implementation PR

_No response_

### Reference Issues

_No response_

### Summary

need to switch between automatic and manual control arduino

### Basic Example

Press button, autonomous robot, press again, manual

### Drawbacks

Hard :(

ZM009, 2023-05-07:
is this basically done

qiugai, 2023-05-07:
Yes finished

ZM009, 2023-05-07:
Good stuff.

Closed by most recent merge

Closed 2023-05-07.

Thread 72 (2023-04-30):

🛠 Fix wiring for sonar sensors

nickkrisulevicz, 2023-04-30:
### Start Date

4/30/2023

### Reference Issues

_No response_

### Summary

The sonar sensors were wired up to Vin which ranges from 7v to 12v. This caused the three sonar sensors to overheat and die. This caused the autonomous code to not work since input from the sonar sensors was not what it needed to be. The sonar sensors need to be replaced, and the wires need to be connected to 5v instead of Vin

### Basic Uses

This will affect the autonomous code's ability to run

ZM009, 2023-05-01:
Sonars were replaced and are fully functional.

Closed 2023-05-01.

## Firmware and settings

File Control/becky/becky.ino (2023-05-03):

#include <SoftwareSerial.h> // module for arduino to use BT
#include <TinyGPS++.h> // module for gps
#include "NewPing.h"

// ---define pins--- //
#define relay_Pin 46
#define LMOTOR_IN1 3
#define LMOTOR_IN2 4
#define LMOTOR_IN3 7
#define LMOTOR_IN4 8
#define RMOTOR_IN1 24
#define RMOTOR_IN2 25
#define RMOTOR_IN3 32
#define RMOTOR_IN4 33

//Sonar sensor pins, accomodates all three current sensors
#define TRIGLEFT 52
#define ECHOLEFT 50
#define TRIGRIGHT 42
#define ECHORIGHT 40
#define TRIGREAR 10
#define ECHOREAR 9
#define MAX_DIST 400
#define TRIG 52
#define ECHO 50
TinyGPSPlus gps;
SoftwareSerial bluetooth(12, 13); // declare bluetooth serial object, with established pins for Rx and Tx 
long tick = 0; // to hold # of times the main loop has been ran through
long max_ticks = 75000; // max amount of ticks to trigger emergency brake and laser disable
bool BTconnected = false; // boolean for bluetooth connection
const byte BTpin = 5; // byte to read bluetooth status from state pin
bool auto_toggle = false; // toggle variable to switch between autonomous
char in_char;
NewPing sonar(TRIG, ECHO, MAX_DIST);
static const int TXPin = 45, RXPin = 44; // gps pins CHANGE -------//
static const uint32_t GPSBaud = 9600;
SoftwareSerial ss(RXPin, TXPin);

//1st sonar sensor (left) is DIGITAL PIN: echo: 50, and trigger: 52
//2nd sonar sensor (right) is DIGITAL PIN: echo: 40, trigger: 42
//3rd sonar sensor (rear) is DIGITAL PIN: echo: 9, and trigger: 10
//New sonar sensor ping initialization
NewPing sonarleft(TRIGLEFT, ECHOLEFT, MAX_DIST);
NewPing sonarright(TRIGRIGHT, ECHORIGHT, MAX_DIST);
NewPing sonarrear(TRIGREAR, ECHOREAR, MAX_DIST);
int distleft, distright, distrear;
void setup(){
	// configure motors with pins
	pinMode(relay_Pin, OUTPUT);
	pinMode (LMOTOR_IN1, OUTPUT);
	pinMode (LMOTOR_IN2, OUTPUT);
	pinMode (LMOTOR_IN3, OUTPUT);
	pinMode (LMOTOR_IN4, OUTPUT);
	pinMode (RMOTOR_IN1, OUTPUT);
	pinMode (RMOTOR_IN2, OUTPUT);
	pinMode (RMOTOR_IN3, OUTPUT); 
	pinMode (RMOTOR_IN4, OUTPUT);
	pinMode(BTpin,INPUT); 
	//Serial.begin(9600); // initialize serial channel
  ss.begin(GPSBaud);
	bluetooth.begin(9600); // initialize bluetooth channel
	Brake(); // inital brake call for safety
    while(!BTconnected){ // wait for HC-05 bluetooth connection
        if(digitalRead(BTpin)==HIGH){
            BTconnected = true;
            in_char == 's';
        }
    }
}

// --------------------main control loop-------------------- //
void loop(){
  while(digitalRead(BTpin)==HIGH){ // only run drive code when connection is active
  in_char == bluetooth.read();
    if(auto_toggle == false || in_char == 'y'){
      Serial.println("manual");
      manual();
    }
    else{
      Serial.println("auto");
      if (in_char == 'y'){
        auto_toggle = false;
        return;
      }
      autonomous();
      //gpsCheck(); breaks code
    }
  }
}

// --------------------robot movement functions-------------------- //
void Forward(){
  digitalWrite(LMOTOR_IN1,LOW); // HIGH,LOW sets the motor fowards
  digitalWrite(LMOTOR_IN2,HIGH); // LIN1 and LIN2 is motor 1(left side)
  digitalWrite(LMOTOR_IN3,LOW);// LIN3 and LIN4 is motor 2(left Side)
  digitalWrite(LMOTOR_IN4,HIGH);
  
  digitalWrite(RMOTOR_IN1,HIGH); // Both left and right side go foward
  digitalWrite(RMOTOR_IN2,LOW);
  digitalWrite(RMOTOR_IN3,HIGH);// RIN1 and RIN2 is motor 3(right side)
  digitalWrite(RMOTOR_IN4,LOW); // RIN3 and RIN4 is motor 4(right side) 
}

void Backward(){ // robot moves backwards
  digitalWrite(LMOTOR_IN1,HIGH); // LOW,HIGH sets the motor backwards
  digitalWrite(LMOTOR_IN2,LOW);
  digitalWrite(LMOTOR_IN3,HIGH);
  digitalWrite(LMOTOR_IN4,LOW);

  digitalWrite(RMOTOR_IN1,LOW); // Both left and right side go backwards
  digitalWrite(RMOTOR_IN2,HIGH);
  digitalWrite(RMOTOR_IN3,LOW);
  digitalWrite(RMOTOR_IN4,HIGH);
}

void Left(){ // robot rotates counter-clockwise (left)
  digitalWrite(LMOTOR_IN1,HIGH); // left side motors go backwards
  digitalWrite(LMOTOR_IN2,LOW);
  digitalWrite(LMOTOR_IN3,HIGH); 
  digitalWrite(LMOTOR_IN4,LOW);

  digitalWrite(RMOTOR_IN1,HIGH); // right side motors go forwards
  digitalWrite(RMOTOR_IN2,LOW);
  digitalWrite(RMOTOR_IN3,HIGH);
  digitalWrite(RMOTOR_IN4,LOW);
}

void Right(){ // robot rotates clockwise (right)
  digitalWrite(LMOTOR_IN1,LOW); // left side motors go forwards,
  digitalWrite(LMOTOR_IN2,HIGH);
  digitalWrite(LMOTOR_IN3,LOW);
  digitalWrite(LMOTOR_IN4,HIGH);

  digitalWrite(RMOTOR_IN1,LOW); // right side motors go backwards
  digitalWrite(RMOTOR_IN2,HIGH);
  digitalWrite(RMOTOR_IN3,LOW);
  digitalWrite(RMOTOR_IN4,HIGH);
}

void Brake(){ // disables all motor movement
  digitalWrite(LMOTOR_IN1,LOW);
  digitalWrite(LMOTOR_IN2,LOW);
  digitalWrite(LMOTOR_IN3,LOW);
  digitalWrite(LMOTOR_IN4,LOW);

  digitalWrite(RMOTOR_IN1,LOW);
  digitalWrite(RMOTOR_IN2,LOW);
  digitalWrite(RMOTOR_IN3,LOW);
  digitalWrite(RMOTOR_IN4,LOW); 
}

/* // NOT USED: with current hardware this turn implementation is sloppy
void ForwardLeft(){ // robot turns left while moving slightly forward at the same time
  digitalWrite(RMOTOR_IN1,HIGH); // right motors go forward
  digitalWrite(RMOTOR_IN2,LOW);
  digitalWrite(RMOTOR_IN3,HIGH);
  digitalWrite(RMOTOR_IN4,LOW);
}

// NOT USED: with current hardware this turn implementation is sloppy
void ForwardRight(){ //  robot turns right while moving slightly forward at the same time
  digitalWrite(LMOTOR_IN1,HIGH); // left motors go forward
  digitalWrite(LMOTOR_IN2,LOW);
  digitalWrite(LMOTOR_IN3,HIGH);
  digitalWrite(LMOTOR_IN4,LOW);
}
*/

// -------------------- laser activation functions --------------------//
void LaserOn(){ // toggles relay pin to enable laser
	digitalWrite(relay_Pin,HIGH);
}

void LaserOff(){ // toggles relay pin to disable laser
	digitalWrite(relay_Pin,LOW);
}

void LaserBurst(){ // enables laser for specified amount of seconds in sleep function, then disables
	digitalWrite(relay_Pin,HIGH);
	delay(3000);
	digitalWrite(relay_Pin,LOW);
}

void RobotBoogie(){ // makes the robot bust a move, used for debugging motor control
  Left();
  delay(250);
  Right();
  delay(250);
  Left();
  delay(250);
  Right();
  delay(250);
  Left();
  delay(250);
  Right();
  delay(250);
  Forward();
  delay(250);
  Backward();
  delay(250);
  Forward();
  delay(250);
  Backward();
  delay(250);
  Forward();
  delay(250);
  Backward();
  delay(250);
	Brake();
}

void manual(){
  in_char = bluetooth.read(); // char variable to store read byte over bluetooth
  auto_toggle = false;   
  if (in_char=='q' || in_char=='l' || in_char=='c'){ // inputs for left turns
    Left();
  }
  else if(in_char=='e' || in_char=='z' || in_char=='r'){ // inputs for right turns
    Right();
  }
  else if(in_char=='b'){ // backwards
    Backward();
  }
  else if(in_char=='f'){ // forwards
    Forward();
  }
  else if(in_char=='s'){ // stops
    Brake();
  }
  else if(in_char=='p'){
    RobotBoogie();
  }
  else if(in_char=='+'){ // laser toggle on
    LaserOn();
  }
  else if(in_char=='-'){ // laser toggle off
    LaserOff();
  }
  else if(in_char == 't'){ // toggle to autonomous
    auto_toggle = true;
  }
}

void autonomous(){
  in_char = bluetooth.read(); // char variable to store read byte over bluetooth
  if (in_char == 'y'){
    auto_toggle = false;
    return;
  }
  //Flags for turn statuses
  bool LeftTurn = false;
  bool RightTurn = false;
  bool Straight = false;
  bool Reversing = false;

  distleft = sonarleft.ping_cm();
  distright = sonarright.ping_cm();
  distrear = sonarrear.ping_cm();

  if(distleft >= 15 && distright >= 15){ //if left and right are clear, drive forward
    //Serial.println("MAIN DRIVE FORWARD CONDITION");
    Straight = true;
    Forward();
    //Serial.println("CALL FORWARD 99");
    Serial.print("Left distance: ");
    Serial.print(distleft);
    Serial.println(" cm");
    Serial.print("Right distance: ");
    Serial.print(distright);
    Serial.println(" cm");
    Serial.print("Rear distance: ");
    Serial.print(distrear);
    Serial.println(" cm");
  }

  Forward();
  //Serial.println("CALL FORWARD 112");
  if(distleft < 15 && distright >= 15){ //if left sensor detects obstacle within 15 cm, turn right
    //Serial.println("LEFT SENSOR IS BLOCKED CONDITION");
    Brake();
    //Serial.println("CALL BRAKE 116");
    Straight = false;
    delay(250);
    //Serial.println("CALL DELAY 119");
    RightTurn = true;
    Right();
    //Serial.println("CALL RIGHT 122");
    Serial.print("Left distance: ");
    Serial.print(distleft);
    Serial.println(" cm");
    Serial.print("Right distance: ");
    Serial.print(distright);
    Serial.println(" cm");
    Serial.print("Rear distance: ");
    Serial.print(distrear);
    Serial.println(" cm");
    delay(500);
    //Serial.println("CALL DELAY 133");
  }
  RightTurn = false;

  Straight = true;
  Forward();
  //Serial.println("CALL FORWARD 139");
  if(distright < 15 && distleft >= 15){ //if right sensor detects obstacle within 15 cm, turn left
    //Serial.println("RIGHT SENSOR IS BLOCKED CONDITION");
    Brake();
    //Serial.println("CALL BRAKE 143");
    Straight = false;
    delay(250);
    //Serial.println("CALL DELAY 146");
    Left();
    //Serial.println("CALL LEFT 148");
    Serial.print("Left distance: ");
    Serial.print(distleft);
    Serial.println(" cm");
    Serial.print("Right distance: ");
    Serial.print(distright);
    Serial.println(" cm");
    Serial.print("Rear distance: ");
    Serial.print(distrear);
    Serial.println(" cm");
    delay(500);
    //Serial.println("CALL DELAY 159");
  }
  LeftTurn = false;

  Straight = true;
  Forward();
  //Serial.println("CALL FORWARD 165");
  if(distright < 15 && distleft < 15){ //if both front sensors are obstructed, drive in reverse
    //Serial.println("BOTH FRONT SENSORS ARE BLOCKED CONDITION");
    Brake();
    //Serial.println("CALL BRAKE 169");
    Straight = false;
    delay(250);
    //Serial.println("CALL DELAY 172");
    Reversing = true;
    Backward();
    //Serial.println("CALL BACKWARD 175");
    Serial.print("Left distance: ");
    Serial.print(distleft);
    Serial.println(" cm");
    Serial.print("Right distance: ");
    Serial.print(distright);
    Serial.println(" cm");
    Serial.print("Rear distance: ");
    Serial.print(distrear);
    Serial.println(" cm");
    if(distrear > 15){ //if rear sensor is blocked, turn right
      //Serial.println("REAR SENSOR IS BLOCKED CONDITION");
      Brake();
      //Serial.println("CALL BRAKE 188");
      Reversing = false;
      RightTurn = true;
      Right();
      //Serial.println("CALL RIGHT 192");
      Serial.print("Left distance: ");
      Serial.print(distleft);
      Serial.println(" cm");
      Serial.print("Right distance: ");
      Serial.print(distright);
      Serial.println(" cm");
      Serial.print("Rear distance: ");
      Serial.print(distrear);
      Serial.println(" cm");
      delay(250);
      //Serial.println("CALL DELAY 203");
      RightTurn = false;
    }
    else{ //if rear sensor is clear, turn right after half second of reversing
      Serial.println("REAR SENSOR IS CLEAR CONDITION");
      delay(500);
      //Serial.println("CALL DELAY 209");
      Reversing = false;
      RightTurn = true;
      Right();
      //Serial.println("CALL RIGHT 213");
      Serial.print("Left distance: ");
      Serial.print(distleft);
      Serial.println(" cm");
      Serial.print("Right distance: ");
      Serial.print(distright);
      Serial.println(" cm");
      Serial.print("Rear distance: ");
      Serial.print(distrear);
      Serial.println(" cm");
      delay(250);
      //Serial.println("CALL DELAY 224");
      RightTurn = false;
    }
  }

  Straight = true;
  Forward();

}

void gpsCheck(){
    if (gps.encode(ss.read()))
        displayInfo();

  if (millis() > 5000 && gps.charsProcessed() < 10){
    bluetooth.println(F("No GPS detected: check wiring."));
    while(true);
    }
}
void displayInfo(){
  bluetooth.print(F("Location: ")); 
  if (gps.location.isValid()){
    bluetooth.print(gps.location.lat(), 6);
    bluetooth.print(F(","));
    bluetooth.print(gps.location.lng(), 6);
  }
  else{
    bluetooth.print(F("INVALID"));
  }
/*
  Serial.print(F("  Date/Time: "));
  if (gps.date.isValid()){
    Serial.print(gps.date.month());
    Serial.print(F("/"));
    Serial.print(gps.date.day());
    Serial.print(F("/"));
    Serial.print(gps.date.year());
  }
  else{
    Serial.print(F("INVALID"));
  }

  Serial.print(F(" "));
  if (gps.time.isValid()){
    if (gps.time.hour() < 10) Serial.print(F("0"));
    Serial.print(gps.time.hour());
    Serial.print(F(":"));
    if (gps.time.minute() < 10) Serial.print(F("0"));
    Serial.print(gps.time.minute());
    Serial.print(F(":"));
    if (gps.time.second() < 10) Serial.print(F("0"));
    Serial.print(gps.time.second());
    Serial.print(F("."));
    if (gps.time.centisecond() < 10) Serial.print(F("0"));
    Serial.print(gps.time.centisecond());
  }
  else{
    Serial.print(F("INVALID"));
  }*/

  Serial.println();
}

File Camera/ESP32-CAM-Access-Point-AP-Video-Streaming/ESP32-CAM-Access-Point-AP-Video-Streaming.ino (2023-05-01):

#include "esp_camera.h"
#include <WiFi.h>
#include "esp_timer.h"
#include "img_converters.h"
#include "Arduino.h"
#include "fb_gfx.h"
#include "soc/soc.h" //disable brownout problems
#include "soc/rtc_cntl_reg.h"  //disable brownout problems
#include "esp_http_server.h"

// Replace with your network credentials
const char* ssid     = "ESP32-Access-Point";
const char* password = "123456789";

#define PART_BOUNDARY "123456789000000000000987654321"

// This project was tested with the AI Thinker Model, M5STACK PSRAM Model and M5STACK WITHOUT PSRAM
#define CAMERA_MODEL_AI_THINKER
//#define CAMERA_MODEL_M5STACK_PSRAM
//#define CAMERA_MODEL_M5STACK_WITHOUT_PSRAM

// Not tested with this model
//#define CAMERA_MODEL_WROVER_KIT

#if defined(CAMERA_MODEL_WROVER_KIT)
  #define PWDN_GPIO_NUM    -1
  #define RESET_GPIO_NUM   -1
  #define XCLK_GPIO_NUM    21
  #define SIOD_GPIO_NUM    26
  #define SIOC_GPIO_NUM    27
  
  #define Y9_GPIO_NUM      35
  #define Y8_GPIO_NUM      34
  #define Y7_GPIO_NUM      39
  #define Y6_GPIO_NUM      36
  #define Y5_GPIO_NUM      19
  #define Y4_GPIO_NUM      18
  #define Y3_GPIO_NUM       5
  #define Y2_GPIO_NUM       4
  #define VSYNC_GPIO_NUM   25
  #define HREF_GPIO_NUM    23
  #define PCLK_GPIO_NUM    22

#elif defined(CAMERA_MODEL_M5STACK_PSRAM)
  #define PWDN_GPIO_NUM     -1
  #define RESET_GPIO_NUM    15
  #define XCLK_GPIO_NUM     27
  #define SIOD_GPIO_NUM     25
  #define SIOC_GPIO_NUM     23
  
  #define Y9_GPIO_NUM       19
  #define Y8_GPIO_NUM       36
  #define Y7_GPIO_NUM       18
  #define Y6_GPIO_NUM       39
  #define Y5_GPIO_NUM        5
  #define Y4_GPIO_NUM       34
  #define Y3_GPIO_NUM       35
  #define Y2_GPIO_NUM       32
  #define VSYNC_GPIO_NUM    22
  #define HREF_GPIO_NUM     26
  #define PCLK_GPIO_NUM     21

#elif defined(CAMERA_MODEL_M5STACK_WITHOUT_PSRAM)
  #define PWDN_GPIO_NUM     -1
  #define RESET_GPIO_NUM    15
  #define XCLK_GPIO_NUM     27
  #define SIOD_GPIO_NUM     25
  #define SIOC_GPIO_NUM     23
  
  #define Y9_GPIO_NUM       19
  #define Y8_GPIO_NUM       36
  #define Y7_GPIO_NUM       18
  #define Y6_GPIO_NUM       39
  #define Y5_GPIO_NUM        5
  #define Y4_GPIO_NUM       34
  #define Y3_GPIO_NUM       35
  #define Y2_GPIO_NUM       17
  #define VSYNC_GPIO_NUM    22
  #define HREF_GPIO_NUM     26
  #define PCLK_GPIO_NUM     21

#elif defined(CAMERA_MODEL_AI_THINKER)
  #define PWDN_GPIO_NUM     32
  #define RESET_GPIO_NUM    -1
  #define XCLK_GPIO_NUM      0
  #define SIOD_GPIO_NUM     26
  #define SIOC_GPIO_NUM     27
  
  #define Y9_GPIO_NUM       35
  #define Y8_GPIO_NUM       34
  #define Y7_GPIO_NUM       39
  #define Y6_GPIO_NUM       36
  #define Y5_GPIO_NUM       21
  #define Y4_GPIO_NUM       19
  #define Y3_GPIO_NUM       18
  #define Y2_GPIO_NUM        5
  #define VSYNC_GPIO_NUM    25
  #define HREF_GPIO_NUM     23
  #define PCLK_GPIO_NUM     22
#else
  #error "Camera model not selected"
#endif

static const char* _STREAM_CONTENT_TYPE = "multipart/x-mixed-replace;boundary=" PART_BOUNDARY;
static const char* _STREAM_BOUNDARY = "\r\n--" PART_BOUNDARY "\r\n";
static const char* _STREAM_PART = "Content-Type: image/jpeg\r\nContent-Length: %u\r\n\r\n";

httpd_handle_t stream_httpd = NULL;

static esp_err_t stream_handler(httpd_req_t *req){
  camera_fb_t * fb = NULL;
  esp_err_t res = ESP_OK;
  size_t _jpg_buf_len = 0;
  uint8_t * _jpg_buf = NULL;
  char * part_buf[64];

  res = httpd_resp_set_type(req, _STREAM_CONTENT_TYPE);
  if(res != ESP_OK){
    return res;
  }

  while(true){
    fb = esp_camera_fb_get();
    if (!fb) {
      Serial.println("Camera capture failed");
      res = ESP_FAIL;
    } else {
      if(fb->width > 400){
        if(fb->format != PIXFORMAT_JPEG){
          bool jpeg_converted = frame2jpg(fb, 80, &_jpg_buf, &_jpg_buf_len);
          esp_camera_fb_return(fb);
          fb = NULL;
          if(!jpeg_converted){
            Serial.println("JPEG compression failed");
            res = ESP_FAIL;
          }
        } else {
          _jpg_buf_len = fb->len;
          _jpg_buf = fb->buf;
        }
      }
    }
    if(res == ESP_OK){
      size_t hlen = snprintf((char *)part_buf, 64, _STREAM_PART, _jpg_buf_len);
      res = httpd_resp_send_chunk(req, (const char *)part_buf, hlen);
    }
    if(res == ESP_OK){
      res = httpd_resp_send_chunk(req, (const char *)_jpg_buf, _jpg_buf_len);
    }
    if(res == ESP_OK){
      res = httpd_resp_send_chunk(req, _STREAM_BOUNDARY, strlen(_STREAM_BOUNDARY));
    }
    if(fb){
      esp_camera_fb_return(fb);
      fb = NULL;
      _jpg_buf = NULL;
    } else if(_jpg_buf){
      free(_jpg_buf);
      _jpg_buf = NULL;
    }
    if(res != ESP_OK){
      break;
    }
    //Serial.printf("MJPG: %uB\n",(uint32_t)(_jpg_buf_len));
  }
  return res;
}

void startCameraServer(){
  httpd_config_t config = HTTPD_DEFAULT_CONFIG();
  config.server_port = 80;

  httpd_uri_t index_uri = {
    .uri       = "/",
    .method    = HTTP_GET,
    .handler   = stream_handler,
    .user_ctx  = NULL
  };
  
  //Serial.printf("Starting web server on port: '%d'\n", config.server_port);
  if (httpd_start(&stream_httpd, &config) == ESP_OK) {
    httpd_register_uri_handler(stream_httpd, &index_uri);
  }
}

void setup() {
  WRITE_PERI_REG(RTC_CNTL_BROWN_OUT_REG, 0); //disable brownout detector
 
  Serial.begin(115200);
  Serial.setDebugOutput(false);
  
  camera_config_t config;
  config.ledc_channel = LEDC_CHANNEL_0;
  config.ledc_timer = LEDC_TIMER_0;
  config.pin_d0 = Y2_GPIO_NUM;
  config.pin_d1 = Y3_GPIO_NUM;
  config.pin_d2 = Y4_GPIO_NUM;
  config.pin_d3 = Y5_GPIO_NUM;
  config.pin_d4 = Y6_GPIO_NUM;
  config.pin_d5 = Y7_GPIO_NUM;
  config.pin_d6 = Y8_GPIO_NUM;
  config.pin_d7 = Y9_GPIO_NUM;
  config.pin_xclk = XCLK_GPIO_NUM;
  config.pin_pclk = PCLK_GPIO_NUM;
  config.pin_vsync = VSYNC_GPIO_NUM;
  config.pin_href = HREF_GPIO_NUM;
  config.pin_sscb_sda = SIOD_GPIO_NUM;
  config.pin_sscb_scl = SIOC_GPIO_NUM;
  config.pin_pwdn = PWDN_GPIO_NUM;
  config.pin_reset = RESET_GPIO_NUM;
  config.xclk_freq_hz = 20000000;
  config.pixel_format = PIXFORMAT_JPEG; 
  
  if(psramFound()){
    config.frame_size = FRAMESIZE_SVGA;
    config.jpeg_quality = 10;
    config.fb_count = 2;
  } else {
    config.frame_size = FRAMESIZE_SVGA;
    config.jpeg_quality = 12;
    config.fb_count = 1;
  }
  
  // Camera init
  esp_err_t err = esp_camera_init(&config);
  if (err != ESP_OK) {
    Serial.printf("Camera init failed with error 0x%x", err);
    return;
  }
  // Connect to Wi-Fi network with SSID and password
  Serial.print("Setting AP (Access Point)…");
  // Remove the password parameter, if you want the AP (Access Point) to be open
  WiFi.softAP(ssid);

  IPAddress IP = WiFi.softAPIP();
  Serial.print("Camera Stream Ready! Connect to the ESP32 AP and go to: http://");
  Serial.println(IP);
  
  // Start streaming web server
  startCameraServer();
}

void loop() {
  delay(1);
}

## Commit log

2022-09-16 arduino code & report from Franchi
2022-09-22 Add files via upload
    modified arduino code for debugging over a serial connection, also initialization for bluetooth connection
2022-09-22 modified arduino code for serial & bluetooth
    arduino code for debugging over a serial connection, also initialization for bluetooth connection
2022-09-28 created python control script, fixed arduino read
    [arduino.ino]
2022-10-05 Pushing current test interface on React-Native
2022-10-05 added necessary packages for nipplejs and react-nipple for a dynamic controller button
2022-10-05 Camera arduino code
2022-10-06 added laser disable safety features
2022-10-11 Husky Lens Code added
2022-11-02 added comments & laser burst function
2022-11-14 Added helper methods for sample bluetooth app
2022-11-14 Added Basic Bluetooth app: Lists Devices, includes a discovery and pairing page
2022-11-16 Adding code for ESP32 camera
2022-11-17 Added Page created to select a device that's been paired with the phone
2022-11-17 Create README for the Camera's usage
    Will include setup and connection for the app.
2022-11-17 Create README for Arduino control functions
2022-11-17 Added Page to communicate with arduino using bytestream
2022-11-30 fixed laser burst & boogie
    [arduino.ino]
2022-12-02 first he discovered a bug, you wont BELIEVE what happened NEXT
    [arduino.ino]
2022-12-08 test file to track new branch
2022-12-15 filters green image on live video
2023-02-04 added state pin check for BT connection
2023-02-08 fixed bluetooth pin definitions
    [arduino.ino]
2023-02-08 Update README.md
    Adding installation instructions - need to update again once the app is at a stage beyond installing on the phone via Flutter command
2023-02-08 fixed green color range, added framework for live detection
2023-02-09 live tracking of green objects in frame
2023-02-15 changed to og laser function
2023-02-22 added directory for sonar branch and a dummy file to use for sonar testing
2023-03-05 Add files via upload
    Added the flowchart diagram and the finite state machine image for the autonomous operation algorithm
2023-03-08 testing code for sonar distance calculation
2023-03-08 added macro definition for max distance of 400cm.
2023-03-19 better esp32 stream program for server
2023-03-31 commented out lines throwing error on compile
    [ESP32-CAM-Access-Point-AP-Video-Streaming.ino]
2023-04-03 fixed server stream program, now works as AP!
    [esp32.ino]
2023-04-04 Added new Objects directory! This has the stl files for the new chassis
    [Becky Chassis - First Design.stl, Becky's Lid - First Design.stl]
2023-04-05 color tracking now prints cordinates of contours
2023-04-05 livestream is filtered to green objects
2023-04-05 Added a wiring document to reference when new chassis is printed
2023-04-05 Added new directory for hardware specifications for the new chassis, etc
2023-04-07 renamed objects file for clarity
    [Becky Chassis - First Design.stl, Becky's Lid - First Design.stl]
2023-04-10 Prints object coordinates to console
2023-04-10 Update README.md
    Added descriptions of app components in the potential case this project is inherited and maintained by another software group.
2023-04-11 Added the 3D models for final design. Also added readme to sonar directory
    [Becky Chassis - Baseplate.stl, Becky Chassis - First Design.stl, Becky Chassis - Laser.stl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]
2023-04-19 changed initial content type and added esp32 AP
2023-04-25 has sonar in it :)
2023-04-27 merged in early sonar toggle
2023-04-30 Autonomous code for three sensors. GarRIT can now merge with the complete .ino file
2023-05-01 merged in toggle (new sonar)
2023-05-24 New Laser Icon!
